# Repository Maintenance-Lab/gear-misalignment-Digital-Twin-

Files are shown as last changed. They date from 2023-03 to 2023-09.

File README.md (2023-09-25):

# gear-misalignment-Digital-Twin-
Code and models for the gear misalignment Digital Twin  
The system is controlled by a pi4 4gb connected to a Odrive motor driver. 
The main script is used to collect data, run the ai and write a .csv.
The other script provided are to control the motors. 
There is also an import folder for the W&B for the ai. 

## Project structure
    ├── README.md                                       
    ├── kill_motors.py                                  <- kills the motors 
    ├── calibration_motor_1.py                          <- calibrates motor for the platform run when using or having wiped the Odrive board
    ├── calibration_motor_2.py                          <- calibrates motor for the platform run when using or having wiped the Odrive board  
    ├── assest                                          <- images
    ├── imports                                         <- contains the models
    │   ├──export.pkl                                   <- first TSAI model for predicting 600 samples                                  
    ├── tsai_loop_V1_local.ipynb                        <- loop to train and save multiple models                
    ├── tsai_V1_local.ipynb                             <- training a model and visualising data 
    CAD files                
    ├── 
# flow shart for main_DigitalTwin.py 
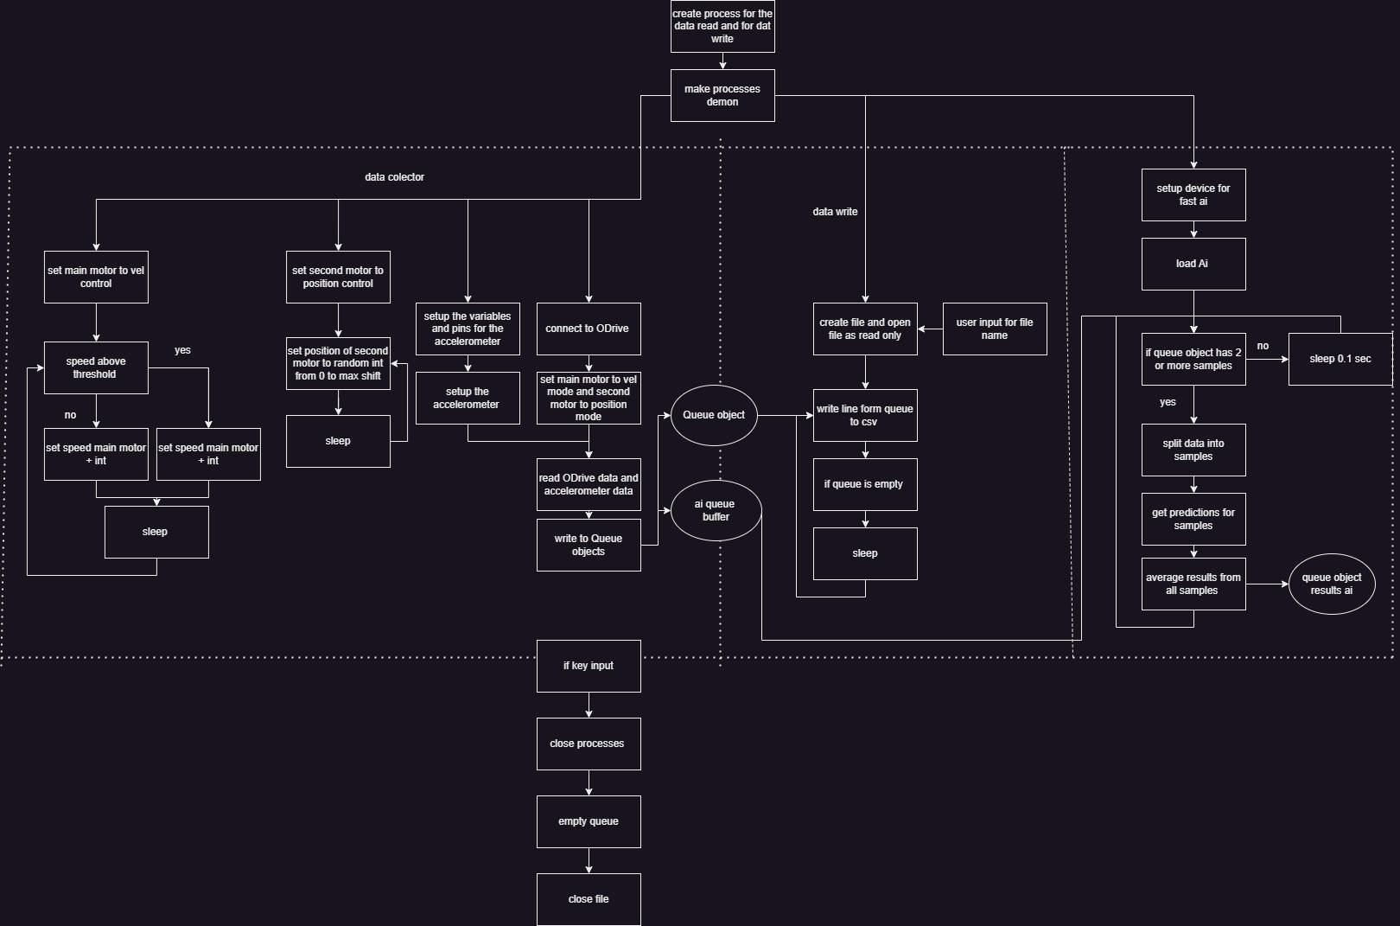
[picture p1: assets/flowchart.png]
main process


# model predictions 
Predictions of the model on the dataset (not actively correcting the position)
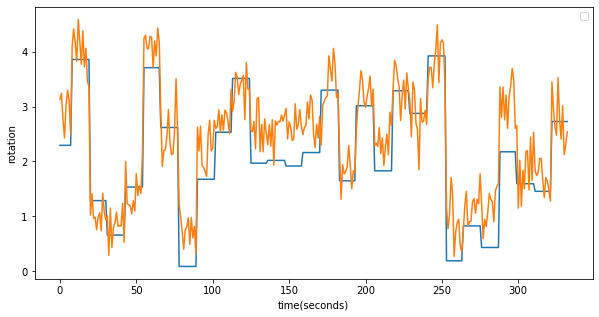
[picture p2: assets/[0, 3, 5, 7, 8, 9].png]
predictions


# calobrating the motors 
The motors are calibrated by hand, the values found are in the calibration_motor.py scripts if there is a problem with the calibration of the motors (motors exit its control mode or jittering) run the calibration scripts. If this doesn't work follow Odrives instructions on calibrating the motors ( https://docs.odriverobotics.com/v/0.5.4/control.html )

# training of the ai
the ai's are train using Fast.ai and TSAI the first script to train and the loop used for the research.

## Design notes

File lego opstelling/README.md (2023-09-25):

# files
Het ontwerp van de logo opstelling is te vinden in de .io file deze kan worden geopend in Lego’s ontwerpprogramma en wordt gebruikt om onderdelen te bestellen.
Instructies voor het bestellen en bouwen zijn te vinden in de pdf’s. 
Een script voor het besturen van de motor en servo.
# To Do:
-	De motoren die bij de opstelling zitten zijn niet compatible met de BaseX. Voor het gebruik van de BaseX zal een EV3 motor moeten worden gebruikt in combinatie met een M5 stack servo voor het bewegen van het platform. 
-	Het eerste plan was de opstelling volledig te runnen van een BaseX en Core2 maar deze kunnen de ai voor de DT niet aan dus er wordt gebruik gemaakt van een pi4. Deze kan de zelfde code gebruiken als grote DT maar heeft een uitbreiding nodig om de motors te besturen. Een mogelijke oplossing is de motors door de BaseX te laten besturen en te communiceren met de BaseX via serial (de base x wacht op serial commandos om de motors aan te sturen en print meetwaardes voor de rotatie van de motors in serial). De andere mogelijke oplossing is over te gaan naar een pi schild dat Lego motoren kan aansturen dit zou makelijker te intergreren zijn met de bestaande code. 
-	De opstelling staat op het moment niet erg stabiel en dit komt door de plaatjes onder te pilaren. Deze zouden beter vervangen kunnen worden door een solide base plate. Ook zouden alle pilaren eigenlijk beter aan elkaar kunnen worden verbonden.

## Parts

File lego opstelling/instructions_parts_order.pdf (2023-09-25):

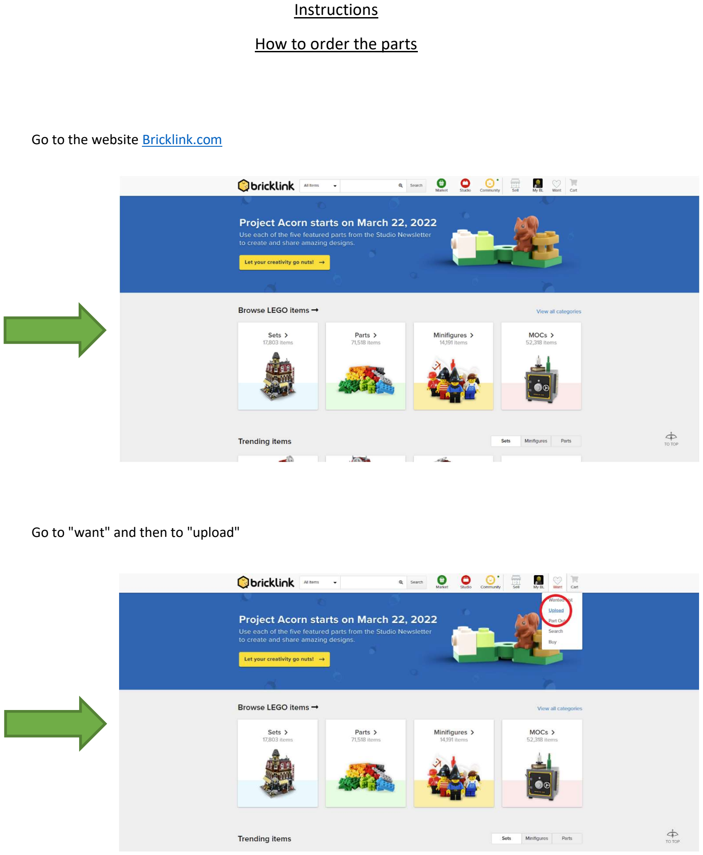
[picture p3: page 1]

### Instructions How to order the parts

Go to the website Bricklink.com

Go to "want" and then to "upload"

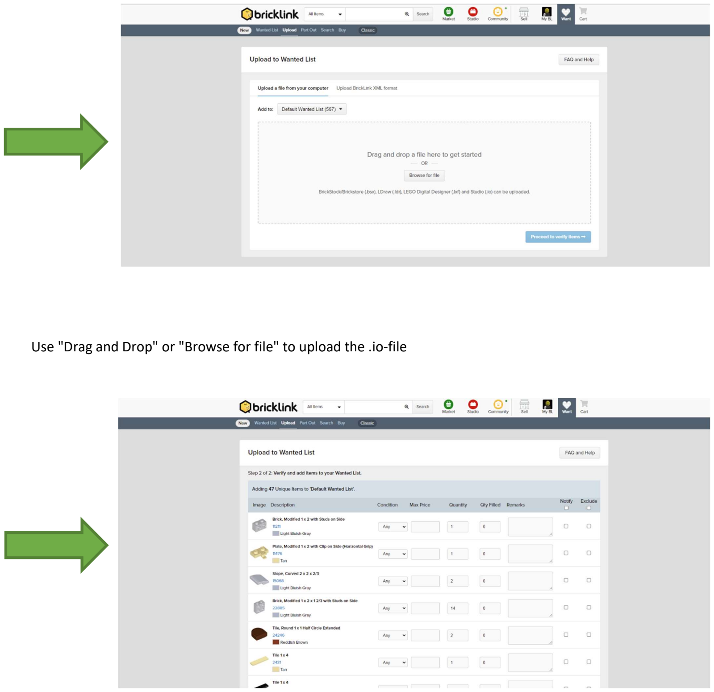
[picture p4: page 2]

Use "Drag and Drop" or "Browse for file" to upload the .io-file

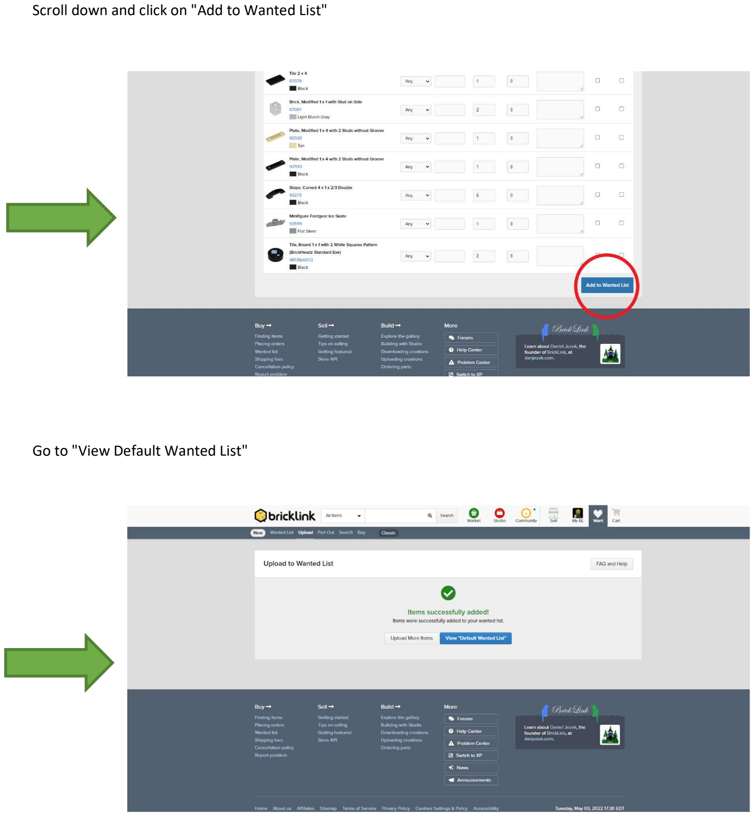
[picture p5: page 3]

Scroll down and click on "Add to Wanted List"

Go to "View Default Wanted List"

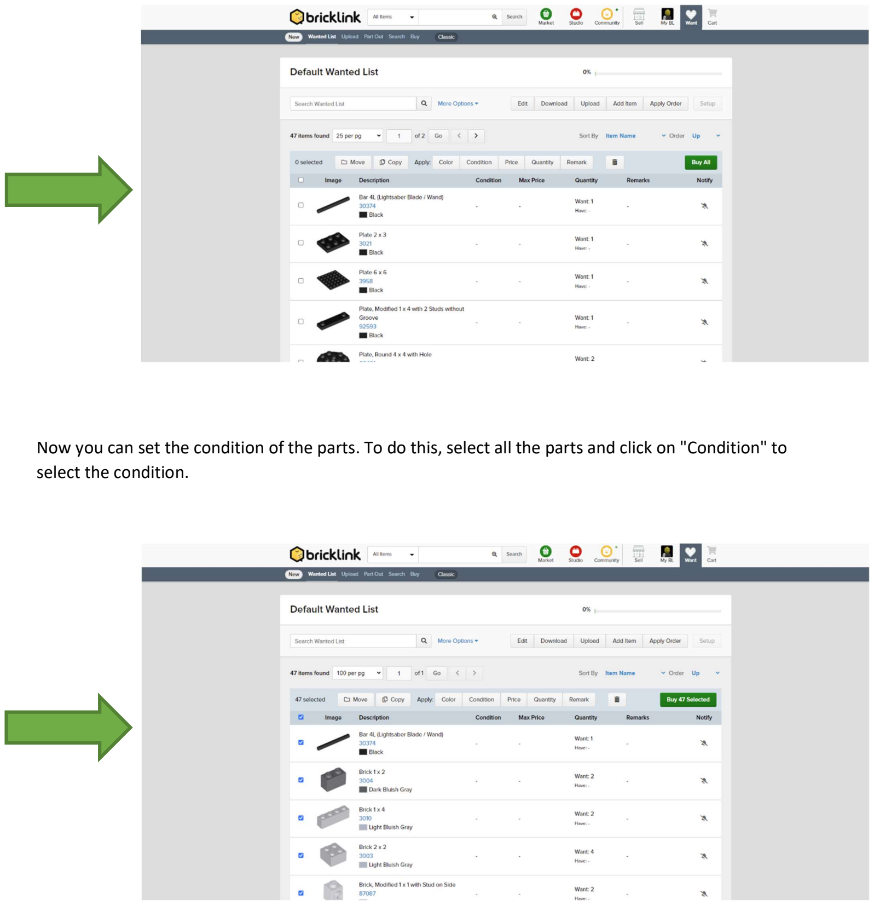
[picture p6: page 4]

Now you can set the condition of the parts. To do this, select all the parts and click on "Condition" to select the condition.

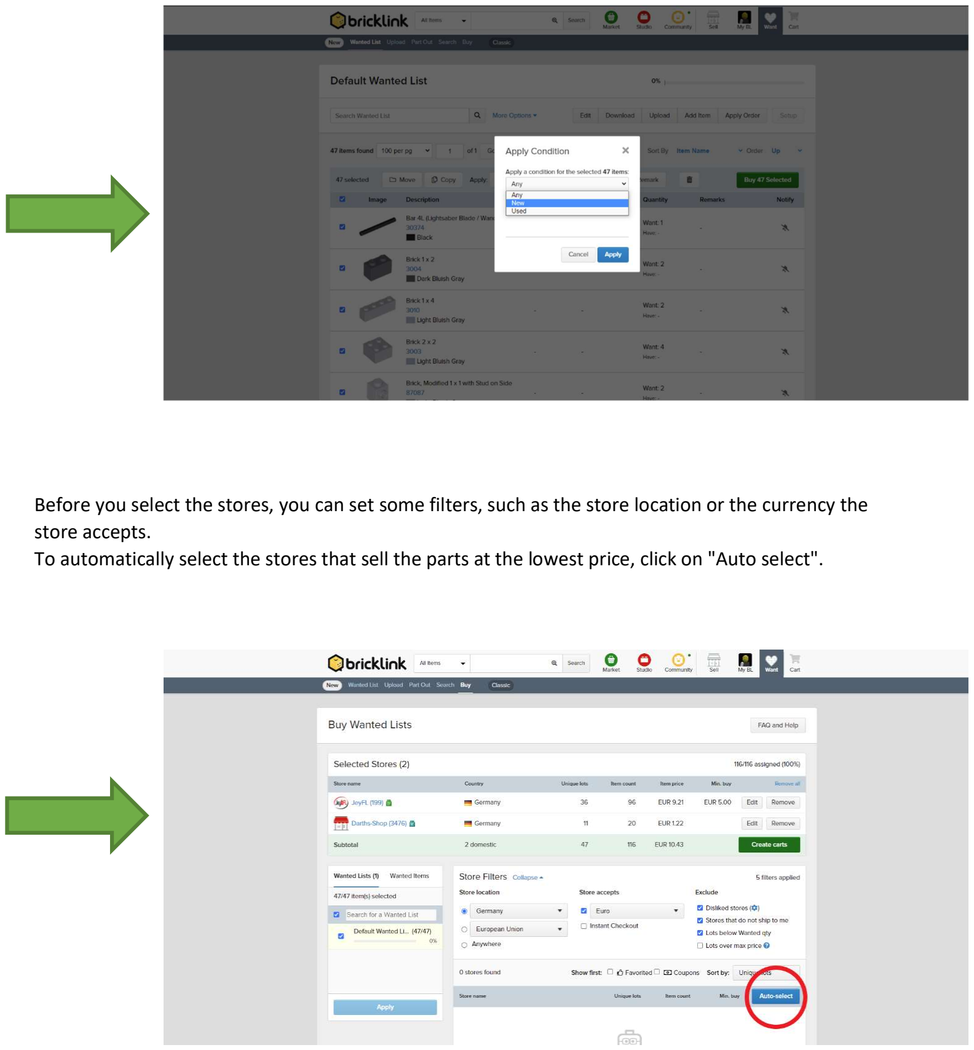
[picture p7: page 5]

Before you select the stores, you can set some filters, such as the store location or the currency the store accepts.
To automatically select the stores that sell the parts at the lowest price, click on "Auto select".

Click on "Create carts" to complete the parts ordering process.

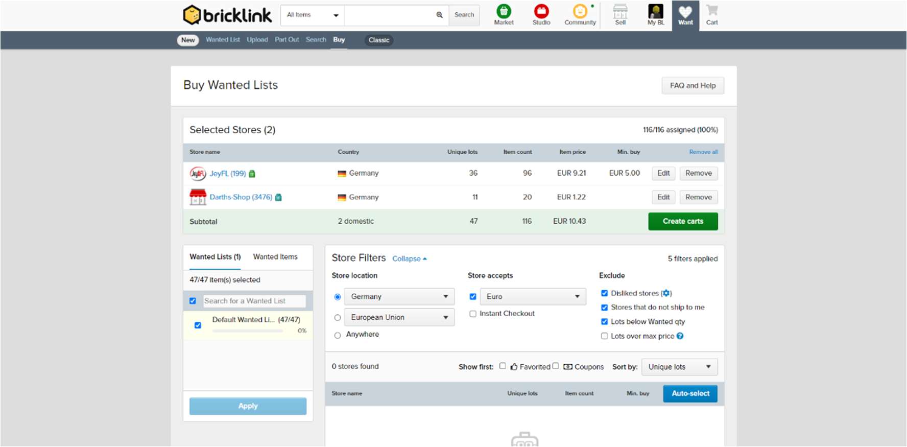
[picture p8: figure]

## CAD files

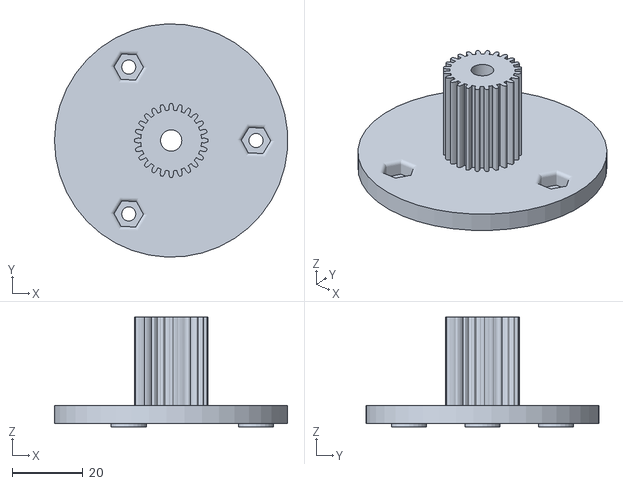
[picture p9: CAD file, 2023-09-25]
CAD files/all STLs DT/top plate carier print 2 keer.stl
65.9 x 66.0 x 31.0

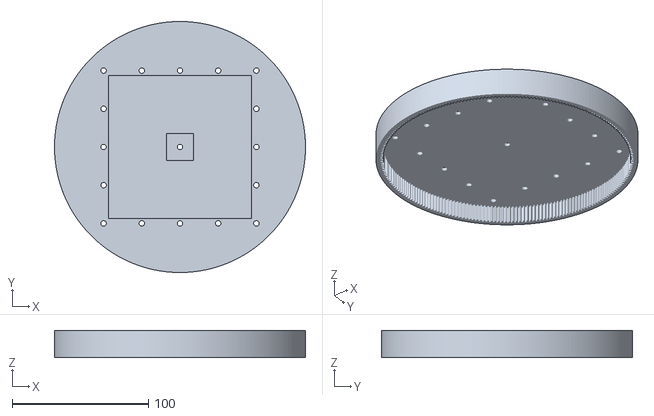
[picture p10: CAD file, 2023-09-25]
CAD files/all STLs DT/topplate.stl
184.0 x 184.0 x 20.0

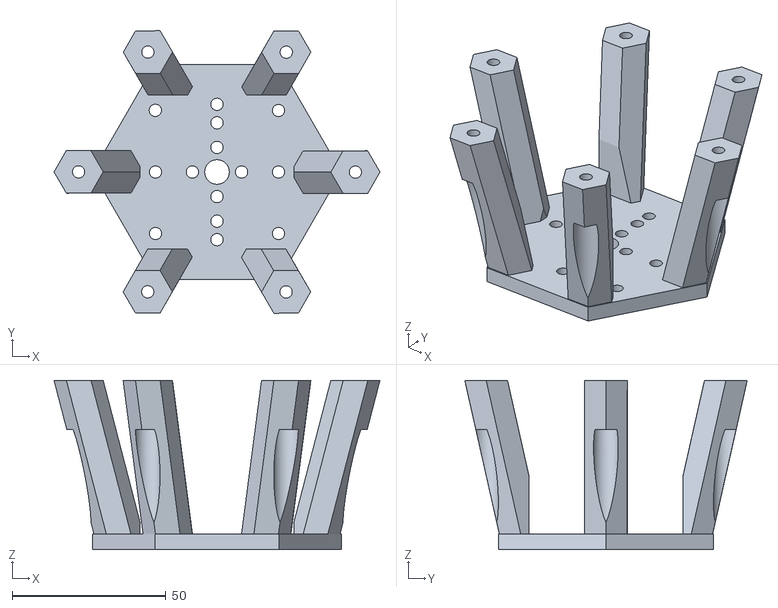
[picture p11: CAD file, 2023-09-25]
CAD files/all STLs DT/top plate motor2 cage.stl
106.0 x 91.9 x 55.0

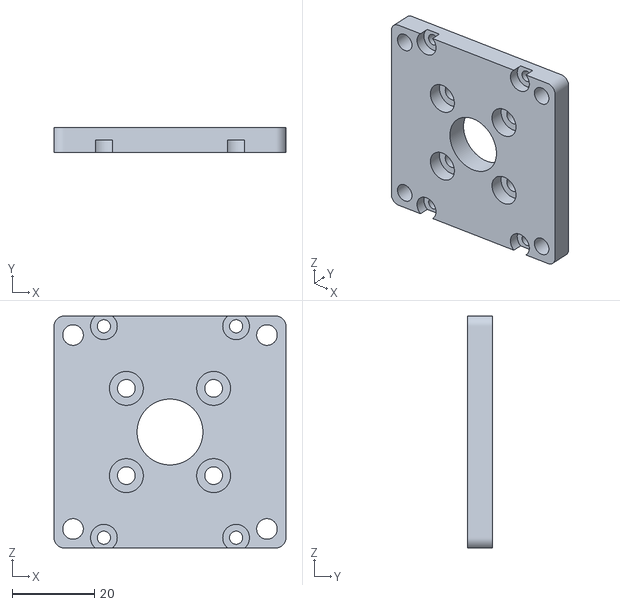
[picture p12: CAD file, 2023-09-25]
CAD files/all STLs DT/motor 1 top plate.stl
56.4 x 6.00 x 56.4

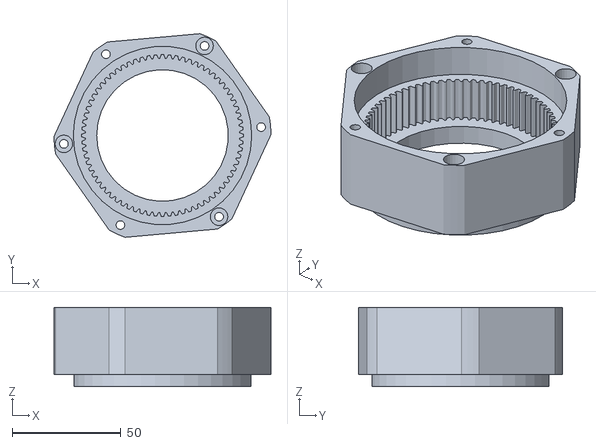
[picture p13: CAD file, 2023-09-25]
CAD files/all STLs DT/ringgear midle layer.stl
100.0 x 93.8 x 36.5

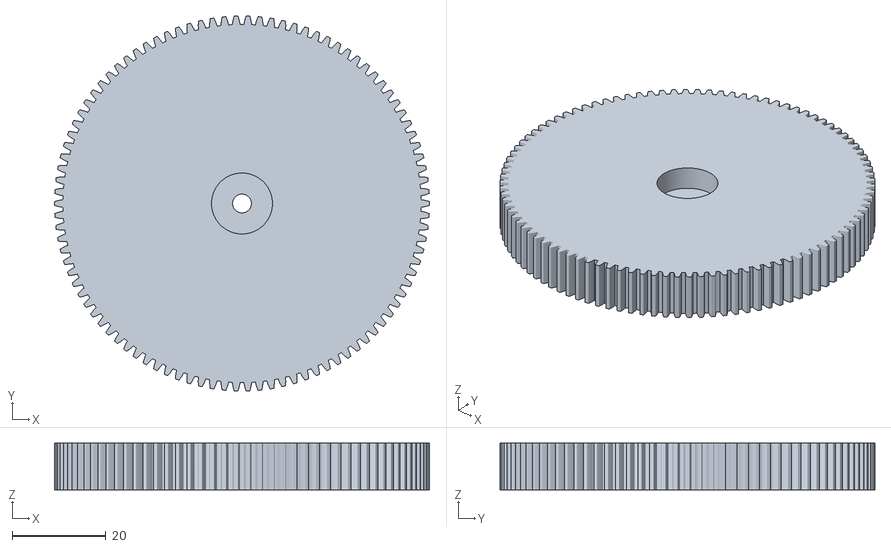
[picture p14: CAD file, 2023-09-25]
CAD files/all STLs DT/big gear print 3 keer .stl
80.0 x 80.0 x 10.0

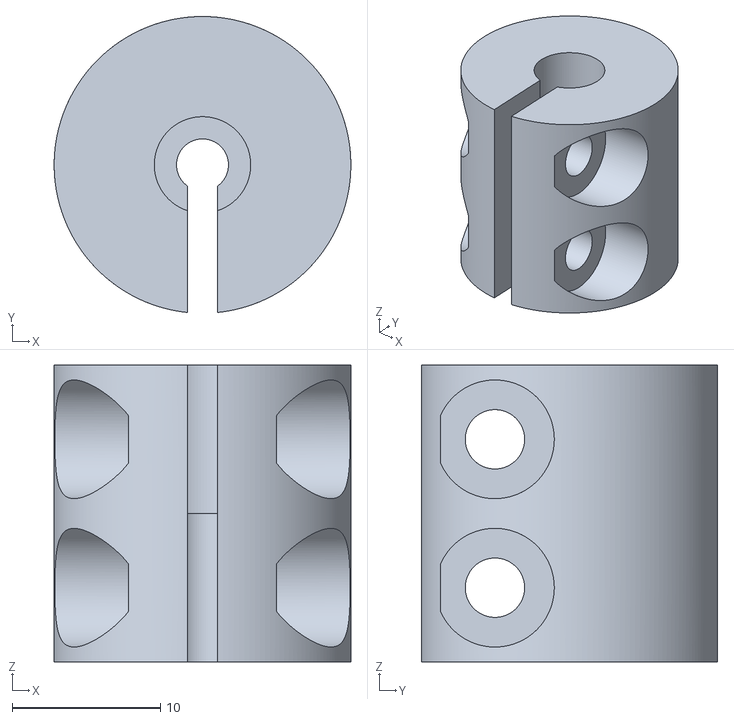
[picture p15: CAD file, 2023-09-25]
CAD files/all STLs DT/3 to 6 mm.stl
20.0 x 19.9 x 20.0

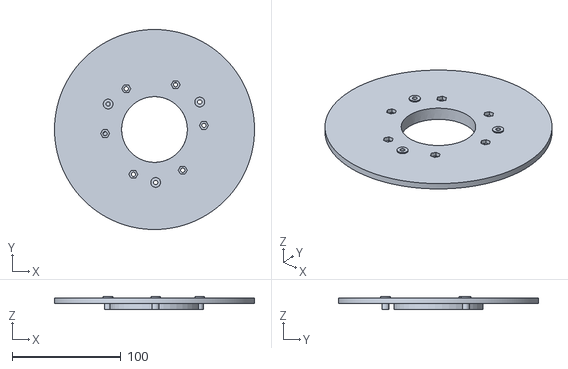
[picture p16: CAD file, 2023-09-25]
CAD files/all STLs DT/bothom plate big gear.stl
184.0 x 184.0 x 11.5

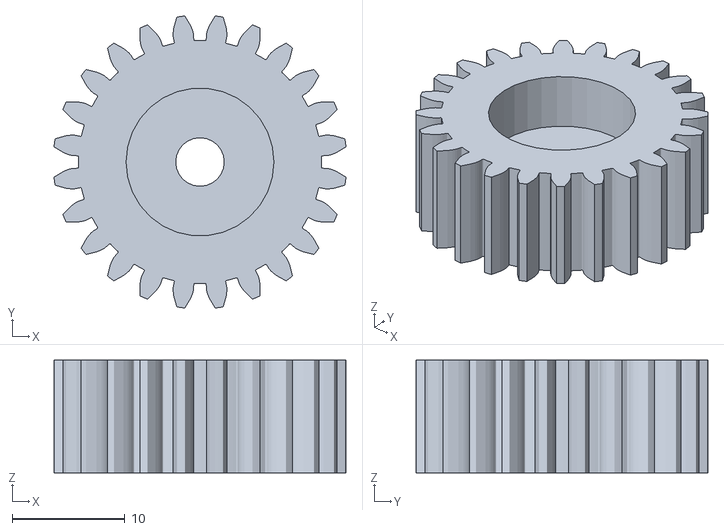
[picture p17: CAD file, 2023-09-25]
CAD files/all STLs DT/plannet gear print 6 keer.stl
25.9 x 25.9 x 10.00

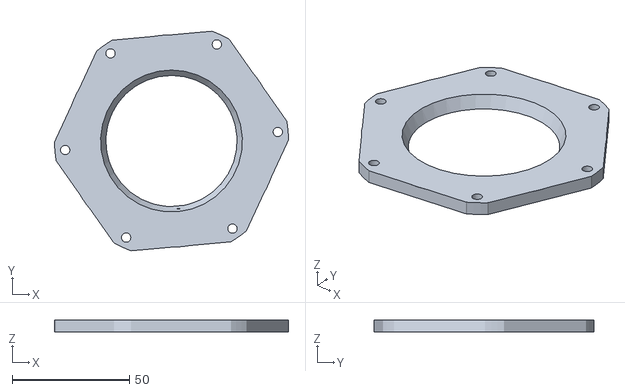
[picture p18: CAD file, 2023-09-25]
CAD files/all STLs DT/bothom carier print 2 keer.stl
100.0 x 93.8 x 5.00

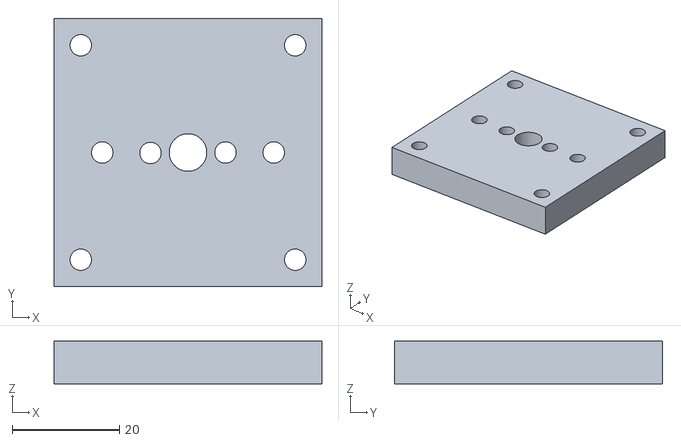
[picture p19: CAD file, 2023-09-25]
CAD files/all STLs DT/encoder plate.stl
50.0 x 50.0 x 8.00

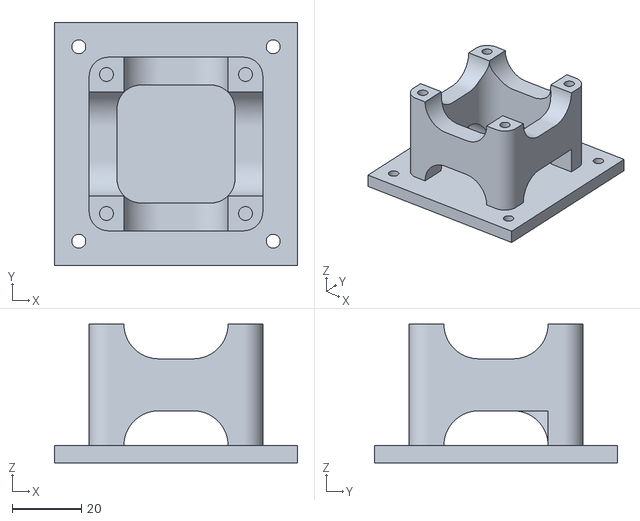
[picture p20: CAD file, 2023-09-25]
CAD files/all STLs DT/motor2 cage .stl
70.0 x 70.0 x 40.0

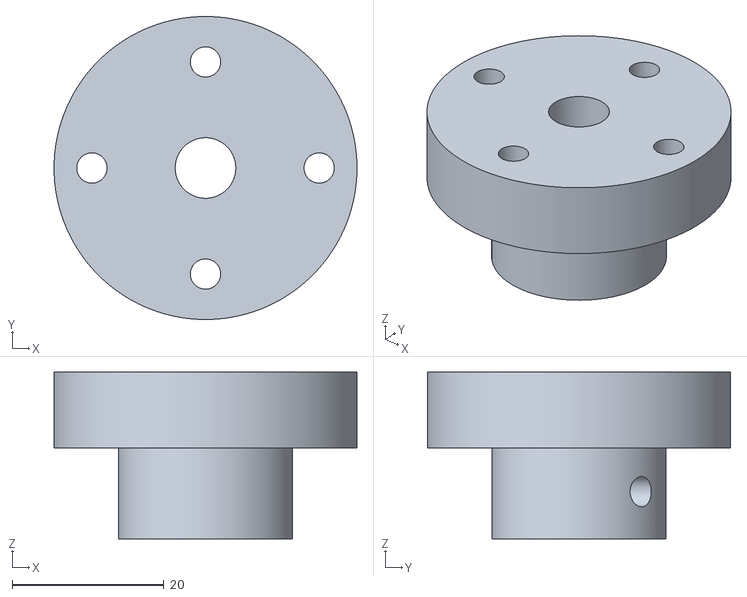
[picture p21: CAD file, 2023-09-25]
CAD files/all STLs DT/gear holder 14_15mm v1.stl
40.0 x 40.0 x 22.0

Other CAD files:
CAD files/Enclosure_motor1.f3d
CAD files/gear motor 1.f3d

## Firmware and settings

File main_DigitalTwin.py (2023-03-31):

import odrive       
import time         
import threading
import multiprocessing as mp
import math         
import random
import pandas as pd
import numpy as np
import matplotlib.pyplot as plt
import csv
#from queue import Queue
from multiprocessing import Queue

# packeges for mpu6050 
import smbus            
from time import sleep          
import math
import RPi.GPIO as GPIO
import sys

# import for tsai and pytorch
from tsai.all import *
computer_setup()
import torch         
import pathlib

'''
set global vars and make Queue objects 
'''
     
stop = 0
q = Queue() # main queue object for data
qs = Queue() # queue for stop signal
q_predict = Queue(maxsize = 1) # queue for broadcasting predictions
q_ai_data = Queue() # window long queue object 

"""
get file name 
"""
filenum = input("name file : ")
time1 = time.time()
#df.to_csv('datadump/data_dump_{}_{}.csv'.format(time1,filenum))
#df.to_csv('datadump/data_dump_{}.csv'.format(filenum))
#df = pd.read_csv('datadump/file.csv',names = ['time','speed','epower'],header=0)


"""
main function odrive and 6050
"""
'''
seperate all interextion to odrive in one process atherwise the
connection can't be shared 
'''
def system(q):
    odrv0 = odrive.find_any()
    """
    fuctions 6050
    """
    # adress 6050
    Device_Address = 0x68
    # I2c adresses for 6050
    PWR_MGMT_1   = 0x6B
    SMPLRT_DIV   = 0x19
    CONFIG       = 0x1A
    GYRO_CONFIG  = 0x1B
    INT_ENABLE   = 0x38
    ACCEL_XOUT_H = 0x3B
    ACCEL_YOUT_H = 0x3D
    ACCEL_ZOUT_H = 0x3F
    GYRO_XOUT_H  = 0x43
    GYRO_YOUT_H  = 0x45
    GYRO_ZOUT_H  = 0x47
    

    bus = smbus.SMBus(1)
    
    # settings 6050
    def MPU_Init():
        bus.write_byte_data(Device_Address, SMPLRT_DIV, 7)
        bus.write_byte_data(Device_Address, PWR_MGMT_1, 1)
        bus.write_byte_data(Device_Address, CONFIG, 0)
        bus.write_byte_data(Device_Address, GYRO_CONFIG, 24)
        bus.write_byte_data(Device_Address, INT_ENABLE, 1)
    
    # read function 6050
    def read_raw_data(addr):
            high = bus.read_byte_data(Device_Address, addr)
            low = bus.read_byte_data(Device_Address, addr+1)
            value = ((high << 8) | low)
            if(value > 32768):
                    value = value - 65536
            return value
    
    # test if odrive is connected    
    def test():
        print(type(odrv0))
        print(odrv0)
        print('test succes')
        odrv0.axis0.controller.input_vel = 0
    #testt = threading.Thread(target=test, args = ())
    #testt.start()
    
    def vel_change():
        '''
        verander snelheid 
        '''
        # the odrive has control modes 0 = voltage 1 = torque 2 = velocity 3 = position
        #odrv0.axis0.controller.config.control_mode = 8
        odrv0.axis0.controller.config.control_mode = 2 
        global stop

        speed = 0
        y = 0
        target = 10
        # variable for the speed of the motor 
        # sine wave form 1 to 6 in steps of 0.2
        while True:
            if qs.empty():
                if speed <= target:
                    target = 6
                    speed = speed + 0.2
                    #print('+')
                else:
                    target = 1
                    #print('-')
                    speed = speed - 0.2
                #print("speed = ",speed)
                #print(odrv0)
                odrv0.axis0.controller.input_vel = speed                 
                y += 0.8
                #print("y =", y)
                time.sleep(3)

            else:
                odrv0.axis0.controller.input_vel = 0
                break
        
        
    def pos_change(q):
        '''
        verander positie
        '''
        # the odrive has control modes 0 = voltage 1 = torque 2 = velocity 3 = position
        odrv0.axis1.controller.config.control_mode = 3 
        pos = 0

        while True:
            global stop
            if qs.empty():
                # set pos to random number between 0 and 4 
                pos = random.uniform(0,4)
                odrv0.axis1.controller.input_pos = pos
                '''
                give update
                '''
                timer = time.process_time()
                speed = odrv0.axis0.encoder.vel_estimate
                pos_estimate_rotate = odrv0.axis1.encoder.pos_estimate
                pos_setpoint = odrv0.axis1.controller.pos_setpoint
                
                print("{:.2f}: rot ={:.4f}, rotsetpoint = {:.4f} speed ={:.4f} ".format(timer,pos_estimate_rotate,pos_setpoint,speed))
                time.sleep(100)
            else:
                odrv0.axis1.controller.input_pos = 0
                break
            
    '''
    read power and save power
    '''
    def read_power(out_q):
        MPU_Init()
        print(ACCEL_XOUT_H,ACCEL_YOUT_H,ACCEL_ZOUT_H)
        while True:
            global stop
            if qs.empty():
                # read data odrive
                timer = time.process_time()
                epower = odrv0.axis0.controller.electrical_power
                ppower = odrv0.axis0.controller.electrical_power
                pos_estimate_main = odrv0.axis0.encoder.pos_estimate
                pos_estimate_rotate = odrv0.axis1.encoder.pos_estimate
                vel_estimate = odrv0.axis0.encoder.vel_estimate
                pos_setpoint = odrv0.axis1.controller.pos_setpoint
                
                # read data 6050
                gyro_x = read_raw_data(GYRO_XOUT_H)
                gyro_y = read_raw_data(GYRO_YOUT_H)
                gyro_z = read_raw_data(GYRO_ZOUT_H)

                accel_x = read_raw_data(ACCEL_XOUT_H)
                accel_y = read_raw_data(ACCEL_YOUT_H)
                accel_z = read_raw_data(ACCEL_ZOUT_H)
                #put data for the writer 
                out_q.put([[timer,pos_estimate_main,pos_estimate_rotate, epower,ppower,vel_estimate,pos_setpoint,gyro_x,gyro_y,gyro_z,accel_x,accel_y,accel_z]])
                # put the data for prediction to go to ai
                q_ai_data.put([[ppower,vel_estimate,gyro_x,gyro_y,gyro_z]])

                      
            else:
                break

    def ai_rot(q):
        while True:
            prediction = q_predict.get()
            pos_estimate_rotate = odrv0.axis1.encoder.pos_estimate
            pos = pos_estimate_rotate - prediction
            if pos <= 4:  
                odrv0.axis1.controller.input_pos = abs(pos)
                print("correcting pos to :", pos, "correct pos = ", pos_estimate_rotate, "estimated pos = ", prediction)
            else:
                print("pos meer dan 4")
            sleep(10)
    #print("system start")
    
    #print(odrv0)
    #print("found motor")
    #pos_estimate_main = odrv0.axis0.encoder.pos_estimate

    #print(pos_estimate_main)
    #print(type(odrv0))
    # start the motors and the data reader
    
    power_thread = threading.Thread(target=read_power, args = (q,))
    pos_thread = threading.Thread(target=pos_change, args = (q,))
    vel_thread = threading.Thread(target=vel_change, args = ())
    ai_rot_thread = threading.Thread(target=ai_rot, args = (q,))
    vel_thread.start()  
    power_thread.start()
    pos_thread.start()
    ai_rot_thread.start()

            
"""
data verwerking 
"""

def datavis(in_q):
    global df
    time.sleep(0.1)
    while True:
            file = open('datadump/data_dump_{}.csv'.format(filenum), 'a')
            write = csv.writer(file)
            while (in_q.qsize() != 0):
                write.writerow(in_q.get()[0])
            time.sleep(2)
            
def ai(q):
    # lead model
    learn = load_learner('/home/hva/Desktop/imports/export.pkl')
    # set window to the length of the models input 
    window = 300
    sample_size = 2
    while True:
        # run inference in a loop
        if q_ai_data.qsize() > 2*window:
            sample_size = math.floor(q_ai_data.qsize()/window)
            print(q_ai_data.qsize())
            # get window of data
            x_data = np.zeros((sample_size, 5, window))
            for j in range(sample_size):
                for i in range(window):
                    dat = q_ai_data.get()
                    x_data[j, :, i] = np.asarray(dat[0])
            #prediction = learn.predict(x_data)
            valid_probas, valid_targets, valid_preds = learn.get_X_preds(x_data, with_decoded=True)
            q_predict.put(torch.mean(valid_probas))
            print("predictions",valid_probas)
            print("mean predictions", torch.mean(valid_probas))
            #print(prediction)
            
        time.sleep(0.1)

'''
start treads
'''

datavis_thread = threading.Thread(target=datavis, args = (q,),daemon=True)
system_thread = mp.Process(target=system, args = (q,),daemon=True)
ai_thread = threading.Thread(target=ai, args = (q,),daemon=True)

datavis_thread.start()
system_thread.start()
ai_thread.start()
'''
stop alles als stop != 0 
'''
stop = input("input graag")
qs.put(5)
print('Done.')

print(q.qsize())
while q.qsize() != 0:
    print(q.qsize())
    time.sleep(0.5)
    
    
exit(0)

    

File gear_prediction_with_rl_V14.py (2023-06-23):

import sys
import csv # Used for writing new data lines
import time
import math
import torch
import smbus # Packages for mpu6050 
import odrive       
import random
import pathlib
import threading
import numpy as np
import pandas as pd
import matplotlib.pyplot as plt
import multiprocessing as mp # The program uses multi processing to run the data collector, writer and RL AI model at the same time with minimal interfence
from multiprocessing import Queue # Queue objects are used to move data between different processes
from sklearn.preprocessing import MinMaxScaler


'''
Set global vars
'''
# Variables to change for the model
model_name = "conv2d_small_test_2"   # Define the name of the model
model_type = "conv2d"       # Determine the model type; simple, lstm, conv1d or conv2d
total_games = 5           # Epochs amount of the neural network
maximum_steps = 10         # Maximum amount of steps each game
# Regularization method: Lower learning rate to get rid of the NaN values in the loss
learning_rate = 0.0015
# Change the speed of the gear setup
max_speed = 5
min_speed = 2
# Activate null model
null_model = False

# Get file name
file_name = input("Insert file name: ")

# Define paths to save data
model_path = "data/models/{}".format(model_name)       # Define the path for the model
rl_path = "data/rl_games_{}.csv".format(file_name)     # Define the path for saving games performed by the model
samples_path = "data/samples_{}.csv".format(file_name) # Define the path for saving all measurements from each sample (~150 samples per second)

start = time.time()  # Record starting time
stop = 0 # Stop variable to end the program

q = Queue()  # Main queue object for data
qs = Queue() # Queue for stop signal
q_ai_data = Queue(maxsize = 150)  # Window long queue object; Remembers only samples as big as the window
q_predict = Queue(maxsize = 1)    # Queue for broadcasting predictions
q_results = Queue(maxsize = 1)    # Queue for the newest position
q_new_game = Queue(maxsize = 1)   # Queue to start a new game

# Action set for the actions
action_set = {
    0: 'forward',
    1: 'backward',
    2: 'stationary'
}
# Moving set for the moving direction
moving_status = {
    0: 'left',
    1: 'right',
    2: 'still'
}


'''
Main thread to run the odrive
All interaction to the odrive needs to be used in one process, because the connection can't be shared between different threads
'''
# Runs the odrive and all functions that use the odrive
def system(q):
    odrv0 = odrive.find_any() # Defines the odrive
    # adress 6050
    Device_Address = 0x68
    # I2c for 6050
    PWR_MGMT_1   = 0x6B
    SMPLRT_DIV   = 0x19
    CONFIG       = 0x1A
    GYRO_CONFIG  = 0x1B
    INT_ENABLE   = 0x38
    ACCEL_XOUT_H = 0x3B
    ACCEL_YOUT_H = 0x3D
    ACCEL_ZOUT_H = 0x3F
    GYRO_XOUT_H  = 0x43
    GYRO_YOUT_H  = 0x45
    GYRO_ZOUT_H  = 0x47
    
    # Define the bus to configure the odrive
    bus = smbus.SMBus(1)
    
    # Configures some ports on the odrive
    def MPU_Init():
        bus.write_byte_data(Device_Address, SMPLRT_DIV, 7)
        bus.write_byte_data(Device_Address, PWR_MGMT_1, 1)
        bus.write_byte_data(Device_Address, CONFIG, 0)
        bus.write_byte_data(Device_Address, GYRO_CONFIG, 24)
        bus.write_byte_data(Device_Address, INT_ENABLE, 1)
    
    # Read the raw data of the odrive
    def read_raw_data(addr):
            high = bus.read_byte_data(Device_Address, addr)
            low = bus.read_byte_data(Device_Address, addr+1)
            value = ((high << 8) | low)
            if(value > 32768):
                    value = value - 65536
            return value

    # Increase or decrease the velocity (speed)
    def velocity_change():
        odrv0.axis0.controller.config.control_mode = 2   # 2 is vel; 1 = torque; 0 is volt; 3 is pos

        speed, y, target = 0, 0, 10
        # Continues to accelerate or decelerate
        while True:
            if qs.empty():
                # Increase speed
                if speed <= target:
                    target = max_speed
                    speed = speed + 0.2
                # Decrease speed
                else:
                    target = min_speed
                    speed = speed - 0.2
                # Set new speed
                odrv0.axis0.controller.input_vel = speed                 
                y += 0.8
                time.sleep(3)
            else:
                # Stop rotating the gear
                odrv0.axis0.controller.input_vel = 0
                break
        
    # Change the position of the rotating gear
    def position_change(q):
        odrv0.axis1.controller.config.control_mode = 3   # 2 is vel; 1 = torque; 0 is volt; 3 is pos
        
        pos, x, target = 0, 0, 0
        # Continues to change the position if a new game is started
        while True:
            if qs.empty():
                # Only changes the position if a new game is started
                if q_new_game.empty():
                    time.sleep(0.1)
                else:
                    # Empty the start game queue
                    empty_queue = q_new_game.get()
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

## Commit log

2023-04-10 Create gear-misalignment-Digital-Twin-.code-workspace
2023-06-23 Full code of the gear prediction with Reinforcement Learning
    [gear_prediction_with_rl_V14.py]
2023-09-25 CAD and Legos
    CAD files, Lego files
    [3 to 6 mm.stl, Enclosure_motor1.f3d, big gear print 3 keer .stl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]
